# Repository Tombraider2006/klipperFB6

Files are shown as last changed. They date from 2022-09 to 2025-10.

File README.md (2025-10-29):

<h3 align="right"><a href="https://www.tinkoff.ru/rm/yakovleva.irina203/51ZSr71845" target="_blank">ваше "спасибо" автору</a></h3>

[**Мануал для тех кто только получил принтер**](/tune-up/newby.md)

[**Что Купить**](what_2_buy/readme.md) всё что надо для того, чтобы принтер  вас любил.

 [**Мануалы по настройке**](tune-up/readme.md) если возник вопрос "как  настроить"  вам сюда. *(фаза активного наполнения.)*

*<h2>**Модификации**</h2>*

   [**Nano4 v3.2 - GD32+CH340, "красная плата"**](GD32.md) - инструкции, марлин. правки под клиппер!

1. [**Marlin 2.1**](marlin/readme.md) модифицированные прошивки марлин, чтоб было на что откатиться, если не понравился klipper.

2.  [**drivers_uart**](https://github.com/Tombraider2006/klipperFB6/tree/main/drivers_uart)
    мануал по распайке драйверов по юарт для платы MKS Robin Nano v4 3.1. избавляемся от ора моторов на высоких скоростях  
3.  [**mcu_uart**](https://github.com/Tombraider2006/klipperFB6/tree/main/mcu_uart)   наглядно о подключении orange pi 3 lts к плате принтера по uart(чтоб провода наружу не торчали)
4.  [**Управление питанием системы, содержащей одноплатный компьютер Orange Pi3 LTS**](https://github.com/evgs/OrangePi3Lts/tree/main/power) 
 
5.  [**bme280**](https://github.com/Tombraider2006/klipperFB6/tree/main/bme280)
     Подключение датчика температуры BME280

6. [**подключение i2c датчиков к плате принтера**](i2c_mcu/readme.md) bme280, lm75a, ht21d и другие.
  
7.   [**clean_nozle**](https://github.com/Tombraider2006/klipperFB6/tree/main/clean_nozle)
     монтаж щетки очистки сопла, модель, макрос.
  
8. [**placement**](https://github.com/Tombraider2006/klipperFB6/tree/main/placement)
   Вариант размещения оборудования внутри принтера. там же необходимые модели для этого.
 
9. [**led_rgb**](https://github.com/Tombraider2006/klipperFB6/tree/main/led_rgb)   Подключение адресной светодиодной ленты к плате принтера

  1. [**Расширение памяти на Orange Pi 3 LTS (и не только)**](https://telegra.ph/Edit-01-28-2) 

   2.  [**Перенос файлов Gcode с внутреннего носителя OrangePi на внешнюю SD карту**](https://telegra.ph/Perenos-fajlov-Gcode-s-vnutrennego-nositelya-OrangePi-na-vneshnyuyu-SD-kartu-02-02)

 8.  [**распиновка платы**](https://github.com/makerbase-mks/MKS-Robin-Nano-V3.X/tree/main/hardware/MKS%20Robin%20Nano%20V3.1_001) - да она под сьемные драйвера в остальном сопадает с мишко6. использовать когда надо узнать какой пин в клиппере написать.
8.   [**Перевод стола на 220V**](/bed220.md)
быстро греем стол медвежонка

*<h3>**Модификации Экструдера**</h3>*

1.  [**biqu_h2**](karas/readme.md)
Модель каретки под экструдер biqu_h2 для FlyingBear Ghost 6.
 Уже 3 версии: под 4010 и 5015 кулеры и Deep версия. Добавлена версия под **V2VS**
1. [**Shark Extruder**](https://github.com/Chiffa-C3/Shark-Extruder) Экструдер разработанный для замены стандартного на принтере FBG6. Используется родной мотор и распространенные запчасти от BMG, встает на родную голову без ее переделок.
2. [**Замена каретки и установка Sailfin Экструдера**](https://youtu.be/aw4aZP5nTXc)
    Под видео есть ссылки на все необходимые файлы и запчасти.

3. [**Голова v2 от RuLED74 на FBG6.**](RuLED74_head_FBG6.rar) E3D V6 хотенд радиатор с гайкой, mrf экструдер(он же sailfin) под круглый мотор, предусмотрен монтаж 3d touch

4. [**Установка E3D V6 хотенда**](https://youtu.be/zrmbZkC-GsI) 
   Новая голова для 6ого призрака от летающих медведей для установки  радиатора e3d с креплением гайкой. Позволяет использовать в дальнейшем распространенные резьбовые термобарьеры. Так же немного переделаны сопла обдува модели, теперь они съемные и не будут мешать, при обслуживании хотенда.
5. [**Проект "Оливье"**](https://telegra.ph/Pechatayushchaya-golova-Olive-12-22) 

6. [**Проект "ZOHAN"**](https://www.thingiverse.com/thing:5883228)
   
   6.1 [**Фидер для ZOHAN**](https://www.thingiverse.com/thing:6153869)  фидер "жучок" из сток шестерёнок остатков набора бмг и двух вентиляторов 4010

7. [**bl-touch**](bltouch/readme.md) варианты крепления датчика на стоковую голову и на BIQU

8. [**FBG6-Condor**](https://github.com/Chiffa-C3/FBG6-Condor) Проект головы "Кондор" с поддержкой датчика Klicky-Probe

9. [**Заказать печатные детали из композита можно здесь**](https://vk.com/enot774rus)

  *<h4>**Про акселерометр**</h4>*

  1. [**Как перестать беспокоится и научится читать графики акселерометра**](accel_graph/readme.md)

 1.  [**adxl345_2_mcu**](https://github.com/Tombraider2006/klipperFB6/tree/main/adxl345_2_mcu) 
    способ подключения акселерометра к плате принтера.

1. [**ADXL 2 orange pi**](https://fdmprint.ru/2022/11/02/podkljuchenie-adxl345-akselerometr-i-orange-pi-3-lts/)
   Подключение акселерометра к OrangePi 3LTS [добавка если не получилось с alt2](adxl345_2_mcu/SPI-CS-FIX.md)

2. [**raspbery pi и ADXL345**](https://telegra.ph/Druzhim-raspbery-pi-s-ADXL345-04-25)Подключение акселерометра к Raspberry PI 

3. [**atmega168-klipper**](https://github.com/iliarub/atmega168-klipper)  ADXL через ардуино

4. **глюки spi** при подключении акселерометра можно устранить по [этому мануалу](https://github.com/orangepi-xunlong/wiringOP) (обычно глюк в 24 не работающем пине исправляется установкой этого git и командой  sudo gpio mode 15 ALT2 

5.[**Настройка Input Shaping в прошивке Marlin**](https://telegra.ph/Nastrojka-Input-Shaping-v-proshivke-Marlin-dlya-Flying-Bear-GHOST-6-02-15) 

*<h2>**Klipper**</h2>*

 1. [**Klipper на Orange Pi3 LTS - легко и быстро**](https://github.com/evgs/OrangePi3Lts/blob/main/sd_images.md) Здесь выложены предварительно настроенные образы Linux (Armbian и Debian) для Orange Pi3 LTS с уже установленным Klipper. Пользователю остаётся только настроить сеть и записать printer.cfg, соответствующий его 3д-принтеру.
 
 2.  [**Настройка Klipper для 3D-принтера FlyingBear Ghost 6 с подключением по USB**](klipper.md) 
 мануал  для совсем новичков, написан при моем содействии.(устарело)

 1. [**klipper_config**](https://github.com/Tombraider2006/klipperFB6/tree/main/klipper_config)
 
    в папке конфиг клиппера на flying bear ghost 6 
  подходит для стокового принтера без доработок, также есть закомментированные разделы небольших доработок. в комментариях файла config.cfg  есть какие то пояснения. читайте внимательно.
*не нужно бездумно копировать всю папку, вам нужен только [конфиг](klipper_config/printer.cfg) остальные файлы просто для сравнения со своими когда вам это будет нужно.*
 3. [**Удаленное управление Klipper**](https://telegra.ph/Udalennoe-upravlenie-Klipperom-cherez-privychnye-interfejsy-04-24)
 4. [**хорошее wiki по клипперу**](https://klipper.wiki/ru/home/initial/peripheral) 
     когда мне лень писать и я пишу что посмотрите сами, лезьте на этот ресурс вероятнее найдете подробную инструкцию

 5. [**wiki по телеграм боту**](https://github.com/nlef/moonraker-telegram-bot/wiki).

6. [**Установка  телеграмм бота на русском**](https://fdmprint.ru/2022/11/03/klipper-telegram-bot-easy/)
   
     конфиг файл бота для  мишки 6 можно скачать [тут](klipper_config/telegram.conf) кладем в папку конфигов не забываем вписать свои данные.

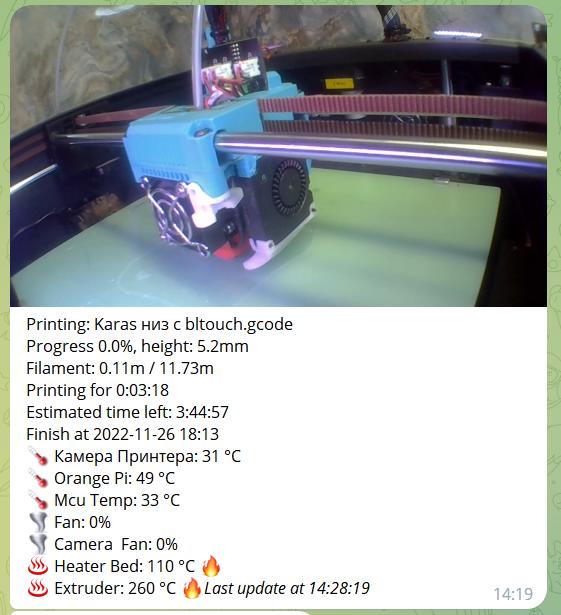
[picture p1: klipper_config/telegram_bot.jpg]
     
7. [**График шейперов сразу в телеграм бот**](/macros/telegram_adxl.md) читаем - делаем,наслаждаемся.

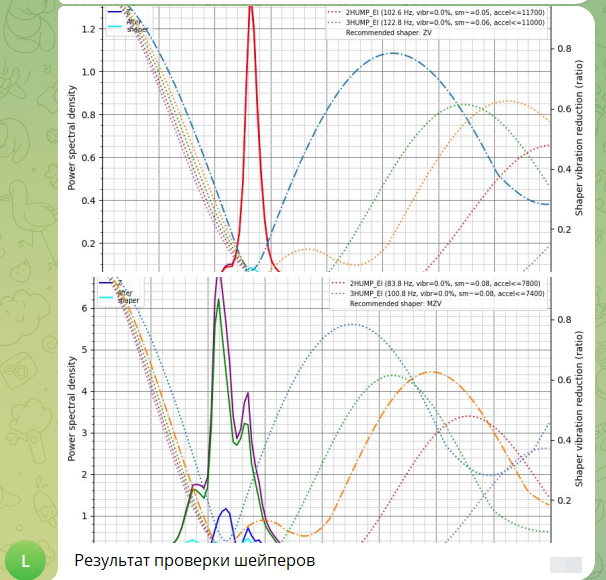
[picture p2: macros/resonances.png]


2. [**Плагин для слайсера CURA с настройками klipper**](https://github.com/jjgraphix/KlipperSettingsPlugin)

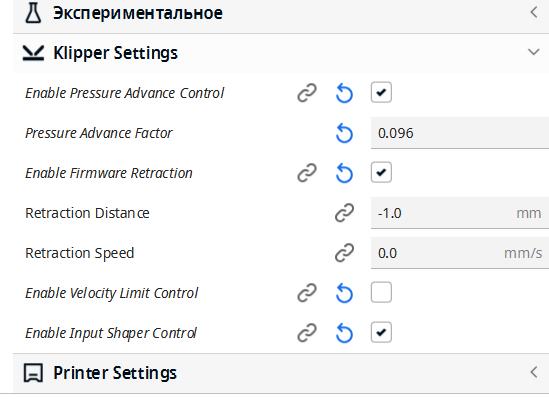
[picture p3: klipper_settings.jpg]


1. Чтобы не бегать с флешкой в Cura есть плагин **Moonraker** ищется через магазин. в нем пишем адрес принтера добавив к нему порт 7125 получится как то так http://ip_printer:7125/  в строке нижней пишем 15 секунд на ожидание ответа от сервера. картинки подключения посмотреть [тут](moonraker.jpg) и [тут](moonaker1.jpg)

 [**Макросы**](macros/readme.md) нужные и не очень

*<h3>**Про экран, стоковый и не только**</h3>*

  Моя рекомендация поставить [7 дюймовый экран](https://www.thingiverse.com/thing:5629418) убрав стоковый

   1. [**Klippersreen**](klippersreen/readme.md) 
Если не запустился сразу *покупной* экран 5 или 7 дюймов.

      2. **Клипперскрин** подключение штатного экрана по [этому мануалу](https://sergey1560.github.io/fb4s_howto/mks_ts35/) в родном мануале совсем невнятная схема подключения [тут](TS35%20Klipper.pdf) тоже самое но чуть понятнее. [**Плата для подключения штатными проводами экрана к вашей PI**](https://github.com/evgs/kross-pi-hat)
      
      3. [**Повышение скорости работы MKS TS35-R**](https://github.com/evgs/OrangePi3Lts/tree/main/fb-st7796-fast)  Актуально для OrangePi3 LTS. На Raspberry PI экран и так работает на высокой частоте SPI

      3. [**Klipper: Debian + KlipperScreen + Экран СТОК FB Ghost6 + MKS TS35-R V2.0**](https://fdmprint.ru/2022/11/19/klipper-debian-klipperscreen-ehkran-stok-fb-ghost6-mks-ts35-r-v2-0/)

      4. **Клипперскрин** если у вас raspberry [тут](https://github.com/willngton/3DPrinterConfig/blob/main/mks_ts35/mks_ts35_guide_archived.md) или [тут](https://github.com/evgs/FBG6-Klipper/blob/main/Klipperscreen-RPI.md)
      5. [**Клипперскрин** на телефоне](https://telegra.ph/KlipperScreen-na-starom-android-telefone-12-16)
   
      6. [**Еще одно руководство по установке клипперскрин на телефон**](https://telegra.ph/KLIPER-NA-ANDROID-TELEFON-03-01)
   
      7. [**Проект "Чувырла"**](chuvir_screen/readme.md) крепление экрана и видеокамеры на место штатного экрана.
     
      8. [**4.3" экран с креплением камеры**](https://www.thingiverse.com/thing:5762517) от наших итальянских пользователей.

*<h2>**остальное**</h2>*

1. [**Охлаждение стола для FBG6**](https://3dtoday.ru/blogs/viknikvvk/oxlazdun-dlya-letayushhego-miski)

2. [**Усиление крепления стола спереди дополнительными валами**](https://www.thingiverse.com/thing:5994260)

3. [**Вариант усиления консольного стола FlyingBear Ghost6 дополнительными валами и двигателем оси Z**](https://www.printables.com/model/1063427-flyingbear-ghost6-auxiliary-z-axis-upgrade) 

4. [**крепление для пишки на магнитах**](https://www.thingiverse.com/thing:5686745) 

5.  [**Автоперезапуск сервиса klipper после включения принтера**](https://mirv.top/2021/10/08/avtoperezapusk-servisa-klipper-posle-vklyucheniya-printera/)

 *<h3>**про камеру**</h3>*
 1. [**ustreamer**](https://fb-waiters.bibirevo.net/klipper/ustreamer#zachem_i_pochemu) 
 Замена\Установка стримингового модуля. Так как mjpg-streamer умер на данный момент, а камеру хочется, читаем, ставим. если что то непонятно есть альтернативный источник [тут](https://fdmprint.ru/2022/11/10/klipper_ustreamer/)

 2.[**Logitech C270 с М12 широкоугольным объективом**](https://telegra.ph/Logitech-C270-s-M12-shirokougolnym-obektivom-03-19) инструкция валидна , [**более правильная модель корпуса**](https://www.thingiverse.com/thing:6440452)

 3. [**RTSP IP камера и Klipper**](https://flyingbear.info/firmware/klipper/IPcam_to_Klipper)

1. **timelapse здорового человека** 

   Многие пользуются функцией таймлапсов которые предоставляет телеграм бот но он ограничен в функионале и не позволяет делать красиво.
если хотите получить действительно хорошие видео рекомендую [вот этот плагин](https://github.com/mainsail-crew/moonraker-timelapse) есть отвод головы на время сьемки кадра, переменный целевой fps и многое другое. посмотрите страничку авторов на гитхабе - не пожалеете. Или читайте инструкцию по установке [тут](https://fdmprint.ru/2022/11/24/klipper-timelapse-intervalnaja-semka-ustanovka-nastrojjka-moonraker-timelapse/)

[**Flyingbear.info**](https://flyingbear.info/firmware/klipper/klipper_more)- полезный ресурс от 5 мишки, там про то как настроить например вебкамеру и не только. многое подойдет на 6 мишку если не забывать что у нас разные платы)

 [**телеграм чат FB6 владельцев и Reborn2**](https://t.me/fbg6_s) где есть многое, если не всё для владельца flying bear ghost 6  он же просто мишка 6. 

`Ставьте звездочку проекту, так будет проще находить владельцам принтера нужную информацию`

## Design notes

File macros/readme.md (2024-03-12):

# Макросы в одном месте

Конечно можно пихать все макросы в основной файл `printer.cfg` но через какое то время вы там совсем потеряетесь. Поэтому лучше добавить строчку `[include имя_файла.cfg]` в любом месте вашего `printer.cfg` где всегда можно отключить или включить его. можно создать папку с макросами и сделать изящнее `[include macros/*.cfg]` и все файлы оттуда будут добавляться в вашу конфигурацию как бы вы их не назвали.

## График шейперов сразу в телеграм бот 

[telegram_adxl.md](telegram_adxl.md) читаем - делаем,наслаждаемся.



> **Ahtung! Attention! Внимание!**
> если есть имена например подсветки в макросе, то они должны совпадать с вашими именами в конфигурационном файле. Читайте документацию!

## Смена Филамента

Чтобы делать полосатенькие модели например так:

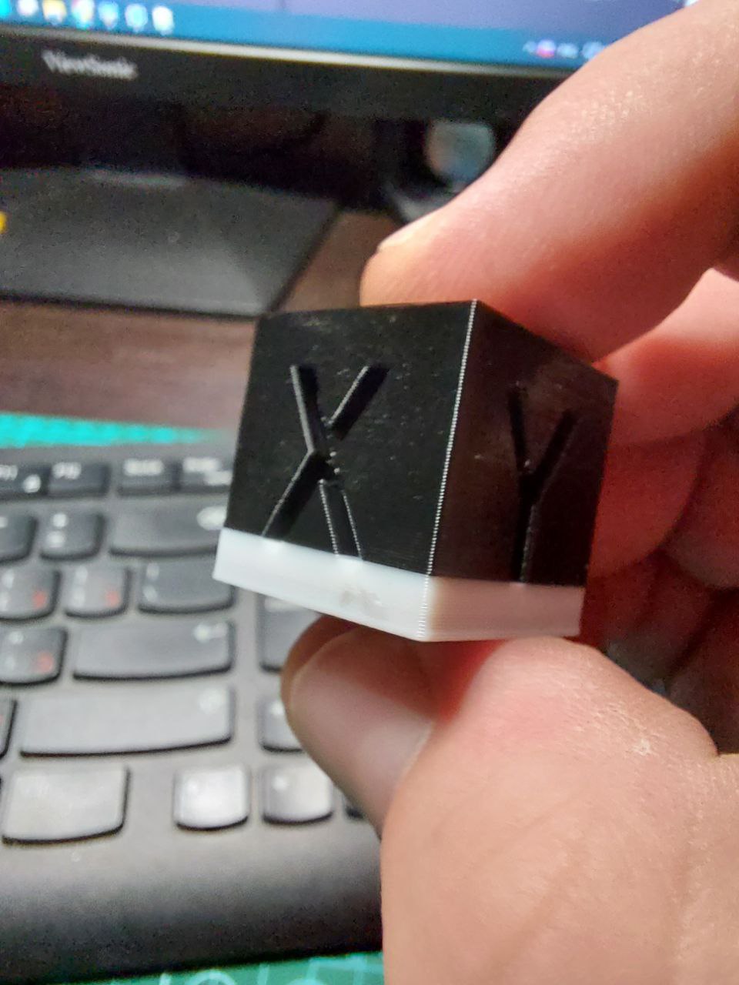
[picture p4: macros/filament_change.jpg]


Варианты:
- [Для стоковой головы FB6](filament.cfg)
- [Для biuu_h2](filament_biqu.cfg)

Составной макрос смены филамента. Ставит на паузу PAUSE, вызывает макрос FILAMENT_UNLOAD для выгрузки филамента, подаёт звуковой сигнал BEEP, COUNTDOWN ждёт 5 минут, пока вы заправите новый филамент в фидер, снова подаёт звуковой сигнал и FILAMENT_LOAD загружает филамент, RESUME запустит печать дальше, если макрос был вызван в процессе печати, например из G-code.

у мишки6 для   [BEEP макроса (скачиваем)](beep.cfg) используется та самая красная лампочка "ханасвист". чтобы ее активировать у вас должен быть раздел в `printer.cfg` если его нет добавляем:
```gcode
[output_pin _Zummer] 
pin: PA2 
```

## Чистка сопла

Этот макрос подьезжает к определенному месту и водит туда сюда по латунной щетке, [подробнее тут](../clean_nozle/readme.md) Быстро скачать [тут](clean.cfg)

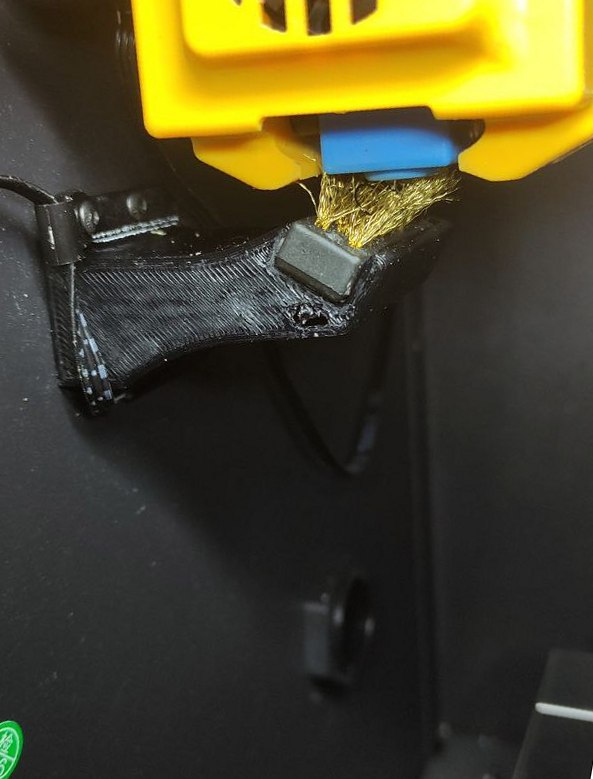
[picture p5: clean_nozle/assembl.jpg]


## Макросы для RGB подсветки

подробнее [тут](../led_rgb/readme.md)

Скачать одним файлом можно [тут](led.cfg)

 

## Адаптивная сетка для стола

 Это почти как обычная сетка для стола, но только "где" и "когда" это необходимо. Иногда я печатаю мелкие детали, иногда печатаю целые пластины, и мне нравится получать точную кровать_сетку (например, 9x9 или больше). Однако это занимает много времени и бесполезно прощупывать всю пластину только на небольшой части посередине. Здесь помогает адаптивная сетка кровати. подробнее [тут](https://github.com/Frix-x/klippain/blob/main/docs/features/adaptive_bed_mesh.md)

## Измерение вибрации

Описание(перевод с гита)

У меня были сильные вибрации на очень специфических скоростях на моей машине (например, 52 мм / с), и я хотел найти все эти проблемные скорости, чтобы избежать их в моем профиле слайсера и, наконец, получить бесшумную машину, о которой я мечтал!

Это полностью автоматизированный рабочий процесс, который работает путем перемещения головки инструмента при использовании акселерометра:

1. Он выполняет последовательность движений по оси, которую вы хотите измерить, с различными настройками скорости, при этом регистрируя глобальные вибрации машины с помощью акселерометра.
Затем он вызывает автоматический скрипт bash, который автоматизирует несколько вещей:
1. он генерирует график вибраций для указанной оси с помощью пользовательского скрипта Python.
Затем он переместит график и связанный с ним архив CSV в папку результатов ADXL .
1. он управляет папкой, чтобы удалить старые файлы и сохранить только набор (по умолчанию три) самых последних результатов.
2. Результаты можно найти в папке результатов ADXL , которая находится непосредственно в корне папки конфигурации, чтобы **обеспечить доступ непосредственно из вашего браузера с помощью файлового менеджера FLuidd/Maisail. SSH не нужен!**
подробнее [тут](https://github.com/Frix-x/klippain/blob/main/docs/features/vibr_measurements.md)

~~в апельсинке есть баг обработки скрипта. добавили паузу при обработке, скачать модифицированный [plot_graphs.sh](../klipper_config_my/scripts/plot_graphs.sh)~~

прочитать про все функции скрипта [тут](https://github.com/Frix-x/klippain/blob/main/docs/features.md)

## Восстановление печати после сбоя питания 

[power_loss.cfg](power_loss.cfg) на данный момент не проверен, стырен [тут](https://github.com/CODeRUS/klipper_config/blob/rumba32/power_loss_simple.cfg)

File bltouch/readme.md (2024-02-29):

[**Вариант монтажа на стоковую голову**](https://www.thingiverse.com/thing:5660302)

[**модель крышки на стоковую голову с креплением под BIQU MicroProbe и с зауженными каналами обдува.**](https://www.printables.com/model/750766-fbg6-biqu-microprobe-mount)

[**Вариант монтажа на стоковую голову продвинутый**](https://www.thingiverse.com/thing:5744744)

Конфиг необходимо править с учетом отступов от сопла до точки замера блтач.!

**Данный конфиг верен для версии головы KARAS_4010 c экструдером BIQU H2 V2**

**Монтаж:**
Подключается в самый нижний левый на плате на нем написано bl-touch, (верхний-сигнал, средний-"+", нижний-земля) который не видно и в концевик "H"(это датчик огня не нужный). контакты концевика (средний-земля, верхний-сигнал).  

**Настройка:**
в секцию `[stepper_z]` необходимо найти исправить!(например видим `endstop_pin: !PC8` исправляем на `#endstop_pin: !PC8`) следующие строки чтобы они выглядели так:

```
#endstop_pin: !PC8 
endstop_pin: probe:z_virtual_endstop
#position_endstop: 0.5
```
(*Внимание! у вас в конфиге уже может быть раздел bed_mesh - его ищем\удаляем и потом вписываем этот*  так же возможно в разделе автоматической настройки  там где "#*#" ищем safe_z_home тоже удаляем )

Создаем новый раздел и вписываем это:

```
[bltouch]

sensor_pin: ^PC4
control_pin: PA8
y_offset: -17.85
z_offset: 2.0
x_offset: 22.65
speed: 10.0
samples: 2
samples_result: median
sample_retract_dist: 3.0
samples_tolerance: 0.1
samples_tolerance_retries: 1

[safe_z_home]
home_xy_position: 105,121                                                       # CAUTION! Depends on probe X/Y offset
z_hop: 10
move_to_previous: True                                                       # Return back ~X0/Y0 after Z0 at center
z_hop_speed: 10
speed: 50
[gcode_macro G29]
gcode:
    BED_MESH_CLEAR
    G28
    BED_MESH_CALIBRATE
    BED_MESH_PROFILE SAVE=name
    SAVE_CONFIG
    BED_MESH_PROFILE LOAD=name

[bed_mesh]
speed: 40
horizontal_move_z: 5 # отступ во время проб по оси Z
mesh_min: 30,10 # CAUTION! = probe_xy = nozzle_xy + offset_xy
mesh_max: 245,185 # стол с учетом сдвига на bltouch
probe_count: 6,4 # здесь мы ставим количество точек проб по икс и по игрек
algorithm: bicubic
fade_start: 1 #на какой высоте начнем выравнивать модель
fade_end: 10 #на этой высоте в мм закончим выравнивать.

[screws_tilt_adjust] # = nozzle_xy = probe_xy - offset_xy
screw4: 5,30 
screw4_name: front left screw
screw1: 210,25
screw1_name: front right screw
screw2: 210,202 
screw2_name: back right screw
screw3: 5,202
screw3_name: back left screw
speed: 100
screw_thread: CW-M4
```
**Как настроить:**

Хоуминг в центре стола, потом двигаете туда сопло, в центр и добиваетесь зазора с которым обычно печатаете. Полученную разницу с нулём по Z вычитаете из того Z-офсет который стоял) по умолчанию ставил 2мм - норм.  И точная калибровка зазора делается при печати, просто ручками подбираее Z-офсет в клиппере и потом опять таки вычитаете из Z-офсета конфига.

**Как проверить отступ датчика от сопла:**(НЕОБЯЗАТЕЛЬНЫЙ ПУНКТ)
положите лист бумаги на стол, прижать прищепками, выровняв по краю. переместить голову над листом и карандашиком отметить где сопло, где кончик датчика. Потом снять лист, померять отступы от сопла.

Юстировка через klippersreen:

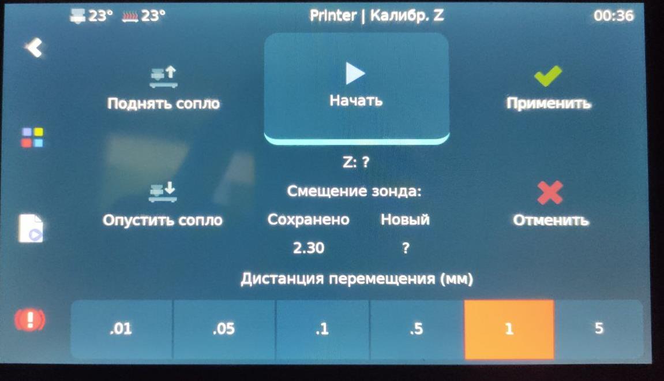
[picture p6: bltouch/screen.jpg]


калибровка стола:

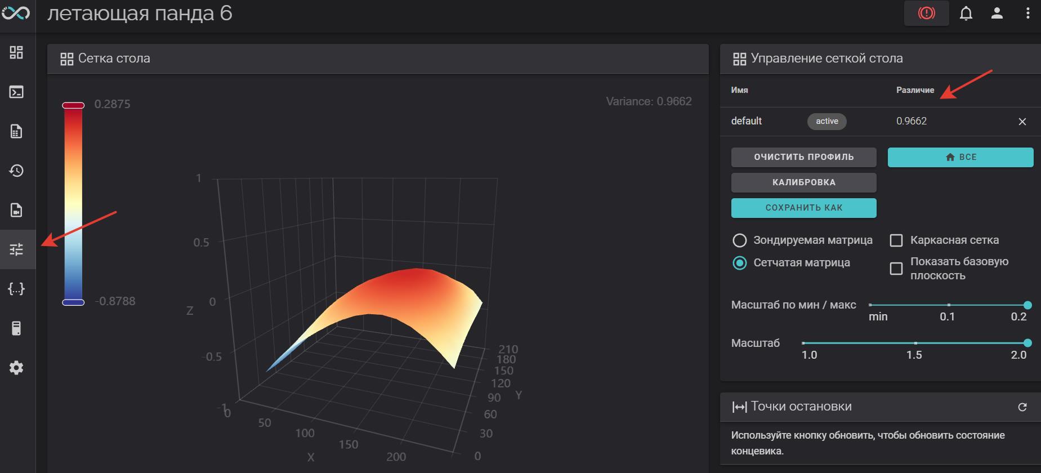
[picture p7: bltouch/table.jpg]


**Настройка винтов по датчику:**
01:20 означает 1 полный оборот и 20 минут по часовой стрелке СW= по часовой стрелке. CCW = против часовой стрелки. 

Очень удобная штука, винты настроить стало гораздо проще.
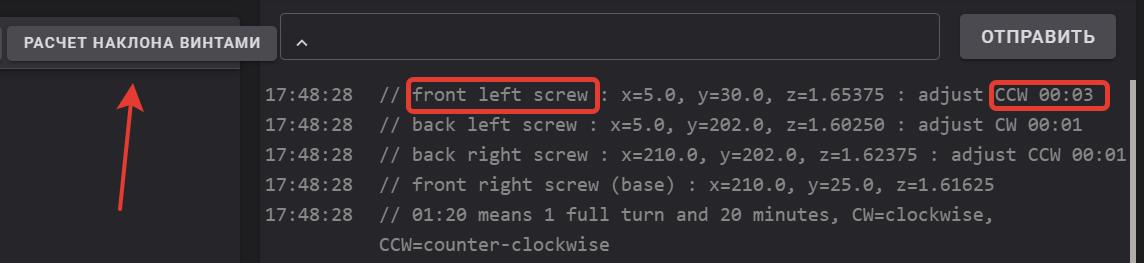
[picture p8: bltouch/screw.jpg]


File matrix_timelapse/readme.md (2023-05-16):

**Таймлапс в стиле фильма матрица** *в разработке*



Если вы уже прошерстили мой Гит вы наверняка уже обзавелись модулем таймлапса но есть у него один недостаток, снимает он с одного ракурса и вот данный раздел призван этот недостаток устранить. 

На данный момент  проект признан жизнеспособным, осталось только твердотельное моделирование и обкатка.

Для реализации нам понадобиться серво самая простая. sg90 подойдет.  в дальнейшем планирую использовать на 270 грудусов, сейчас пока на время разработки используется 180 градусов, подключить ее достаточно просто, у нее три вывода G - земля, VC  5 вольт, и сигнал. ничего не напоминает? да, это практически любой разъём в нашей плате) я использовал `PA8` 3d touch. 

желтый провод сигнал красный 5 вольт и черный или коричневый земля.  цепляем к принтеру. 
в printer.cfg добавляем раздел:

```
[servo matrix]
pin: PA8 #  пин на плате
maximum_servo_angle: 180 # градус сервы
minimum_pulse_width: 0.0008 # по умолчанию 0.001 тут можно поиграться когда серва не поворачивается на полную
maximum_pulse_width: 0.0025 # по умолчанию 0.002 важно не только уменьшать но и увеличивать. тоесть играем парой значений одновременно
initial_angle: 0 # не меняем. это стартовый угол при загрузке принтера
```
После того как подсоеденили и прописали можем проверить. В консоли принтера пишем: `SET_SERVO SERVO=matrix ANGLE=90` дальше пробуем максимальные углы, меняем размер импульсов. для этого можно использовать команду  `SET_SERVO SERVO=matrix WIDTH=0.001`  значения выбирайте сами,  0 выключит серву и можно подвигать руками...

Как наиграетесь можно написать макрос. у меня в `printer.cfg` есть строчка `[include macro.cfg]` и рядышком файл рядышком с таким же именем macro.cfg куда я записываю макросы чтоб они мне не мешали читать конфиг в минуты раздумий)

Итак макрос нам нужен для того чтобы посчитать общее количество слоев и номер текущего слоя  и вычислить градус на какой повернуть серву чтобы вначале был 0, а в конце 180\270 градусов соответсвенно.  спасибо неравнодушным людям которые за несколько потных дней сваяли нам вот такой макрос:

```gcode
[gcode_macro BEGIN_LAYER]
description: Start a new layer and notify system
gcode:

  {% set CUR  = params.NUM|default(0)|float + 1 %}
  {% if params.COUNT and params.COUNT != 0 %}
        {% set TOTAL = params.COUNT|default(0)|float %}
  {% elif printer["gcode_macro middle"].total_layer and printer["gcode_macro middle"].total_layer!= 0 %}
        {% set TOTAL = printer["gcode_macro middle"].total_layer %}
  {% else %}
         { action_respond_info("COUNT of Total layers is required!") }
  {% endif %}

  SET_GCODE_VARIABLE MACRO=middle VARIABLE=cur_layer VALUE={CUR}
  SET_GCODE_VARIABLE MACRO=middle VARIABLE=total_layer VALUE={TOTAL}
  {action_respond_info("BEGIN CUR: %s TOTAL: %s" % (CUR, TOTAL))}

[gcode_macro middle]
description: Variable_storage
variable_cur_layer: 0
variable_total_layer: 0
gcode:
#    {action_respond_info("MIDDLE TOTAL: %s TOTAL: %s" % (CURRENT_LAYER, TOTAL_LAYER))}

[gcode_macro MATRIX]
gcode:
    {% set CURRENT_LAYER = printer["gcode_macro middle"].cur_layer %}
    {% set TOTAL_LAYER = printer["gcode_macro middle"].total_layer %}

    {% set angle_move = 180 / TOTAL_LAYER * CURRENT_LAYER %} #задаем переменную сдвига на слой. вот здесь и задаем свою серву 180 или 270 градусов.
 #   { action_respond_info("MATIRIX TOTAL: %s CUR: %s" % (TOTAL_LAYER, CURRENT_LAYER)) } #вывод в консоль текущего слоя и всего слоев
 #   { action_respond_info("angle %s" % angle_move) } # вывод в консоль текущего угла
    SET_SERVO SERVO=matrix ANGLE={angle_move} #4 макрос сдвига
```
Для того чтобы он заработал нам необходимо сделать так чтобы слайсер нам посылал номера слоеев и их общее количество. (*найдутся умники которые мне скажут что клиппер и так знает количество слоев но это не так, достаточно часто цифры там могут быть сильно далеки от реальных.*) 

В Cura нам надо найти раздел Расширения > Пост-обработка Изменить G-код.

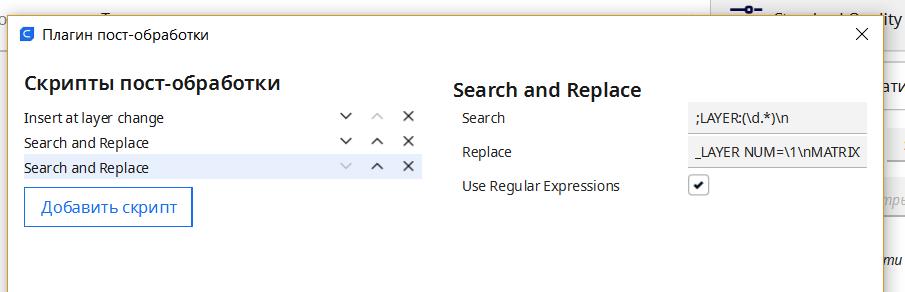
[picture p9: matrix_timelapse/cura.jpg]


Найти раздел `search and replace` и вписать в первую строчку:
`;LAYER_COUNT:(\d.*)\n` 

а во вторую: `;LAYER_COUNT:\1\nBEGIN_LAYER COUNT=\1\n`

Не забываем ставь галочку как на картинке "использовать регулярные выражения"

теперь открываем еще раз `search and replace` 

и теперь в первую строку копируем это: `;LAYER:(\d.*);\n`

во вторую это: `;LAYER:\1;\nBEGIN_LAYER NUM=\1\nMATRIX\n`

Если у вас Prusa Slicer:

в раздел **before layer change G-code** вписать:
``` 
BEGIN_LAYER NUM={layer_num} COUNT={total_layer_count};
matrix;
```
Нарезаем модель, радуемся. 
Для того чтобы всё это заработало нам нужна модель. 
А вот её как раз нет) ждемс или моделируем сами)

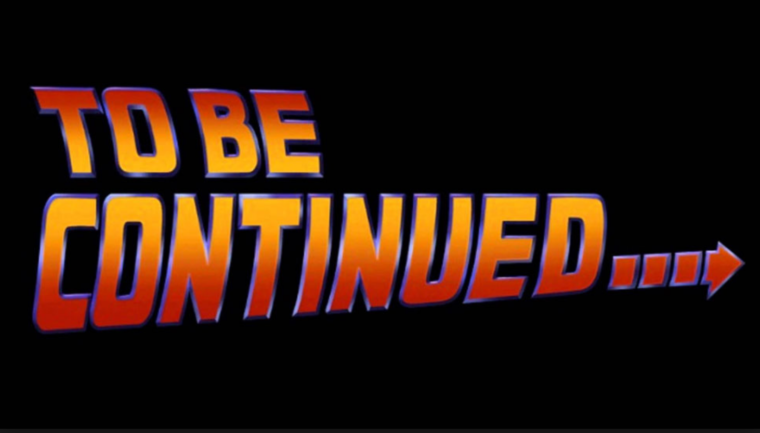
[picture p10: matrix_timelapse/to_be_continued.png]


TEST!!! NOT USE!!!!!

тест, не трогать не использовать. деальнейший код просто обсуждение разработки!!!!

```extratmc
[manual_stepper matrix]
step_pin: PD15
dir_pin: PA1
enable_pin: !PA3
microsteps: 16
rotation_distance: 5.625
full_steps_per_rotation: 200
velocity: 15
accel: 1000
#endstop_pin: !PC8 # раскоментировать при наличии концевика
position_max: 455 # надо померять расстояние и поставить чуть меньше

[gcode_macro BEGIN_LAYER]
description: Start a new layer and notify system
gcode:

  {% set CUR  = params.NUM|default(0)|float + 1 %}
  {% if params.COUNT and params.COUNT != 0 %}
        {% set TOTAL = params.COUNT|default(0)|float %}
  {% elif printer["gcode_macro middle"].total_layer and printer["gcode_macro middle"].total_layer!= 0 %}
        {% set TOTAL = printer["gcode_macro middle"].total_layer %}
  {% else %}
         { action_respond_info("COUNT of Total layers is required!") }
  {% endif %}

  SET_GCODE_VARIABLE MACRO=middle VARIABLE=cur_layer VALUE={CUR}
  SET_GCODE_VARIABLE MACRO=middle VARIABLE=total_layer VALUE={TOTAL}
  {action_respond_info("BEGIN CUR: %s TOTAL: %s" % (CUR, TOTAL))}

[gcode_macro middle]
description: Variable_storage
variable_cur_layer: 0
variable_total_layer: 0
gcode:
#    {action_respond_info("MIDDLE TOTAL: %s TOTAL: %s" % (CURRENT_LAYER, TOTAL_LAYER))}

[gcode_macro MATRIX]
gcode:
    {% set CURRENT_LAYER = printer["gcode_macro middle"].cur_layer %}
    {% set TOTAL_LAYER = printer["gcode_macro middle"].total_layer %}

    {% set angle_move = 450 / TOTAL_LAYER * CURRENT_LAYER %} #задаем переменную сдвига на слой.  первая цифра максимальное расстояние по балке
 #   { action_respond_info("MATIRIX TOTAL: %s CUR: %s" % (TOTAL_LAYER, CURRENT_LAYER)) } #вывод в консоль текущего слоя и всего слоев
 #   { action_respond_info("angle %s" % angle_move) } # вывод в консоль текущего угла
    MANUAL_STEPPER STEPPER=matrix MOVE={angle_move} SPEED=5 #4 макрос сдвига

```

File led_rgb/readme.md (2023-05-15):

**Установка адресной светодиодной ленты.** 

Недостатки штатной ленты принтера ясны каждому владельцу, черный цвет стенок, 
темная поверхность ультрабазы, эффективно поглощают свет и рассмотреть что-то, даже в свете ленты, которая светит абы как, достаточно проблематично.
К сожалению компактность корпуса и необходимость снимать боковую крышку сдвигом вниз, в случае нужды доступа к плате принтера, не позволяют закрепить ленты.
Поэтому решение комплексное и довольно накладное. первая часть описана в разделе  [placement](https://github.com/Tombraider2006/klipperFB6/tree/main/placement)  которая позволяет установить дополнительный блок питания и хост внутри корпуса.
 Вторая часть это подключение адресной ленты. для этого есть штатный разьем неопиксель *PE6* на плате. в который воткнута штатная подсветка, его и используем. 
 у меня было несколько этапов и я сделал два канала подключения. я задействовал штатный разьем для подключения подсветки в голову экструдера,
 а основной свет запитал из разьема 3d-touch *PA8* который все равно некуда сунуть с нашей компоновкой. Я опишу штатный случай и все дальнейшие инструкции для штатного разъема.
 
 **update** (*относится к платам от MKS*) по неопикселю есть лайфхак в виде подтягивающего резистора 4.7К, который ставится на ленту (или в разъём) между сигнальным проводом и +5В. (помечен звездочкой)
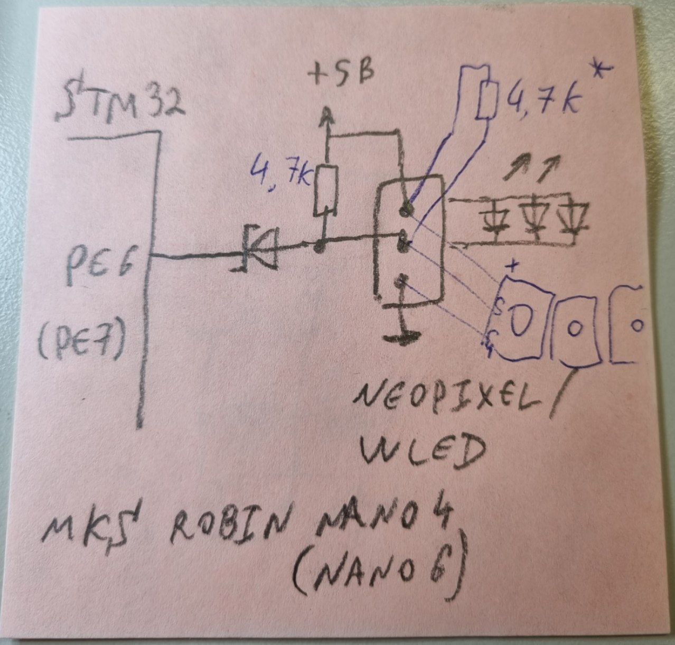
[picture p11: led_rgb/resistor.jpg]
 

 значок подтягивающего резистора в клиппере его не заменит, так как Во-первых, внутренняя подтяжка слишком слабая (~50К), во-вторых, не с той стороны относительно диода (на схеме). Без него напряжение нарастает недостаточно быстро и стабильность работы будет определяться только производителем неопикселей. После распайки резистора получится итоговое сопротивление меньше, ток больше, скорость нарастания напряжения увеличивается.

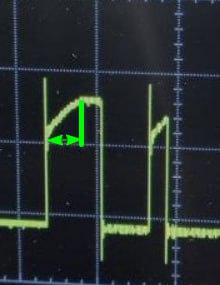
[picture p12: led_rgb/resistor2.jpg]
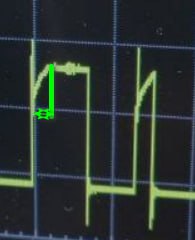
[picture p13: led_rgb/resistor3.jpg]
 

  **немного теории**
 
  Команды в ленте передаются от диода к диоду, паровозиком.
  У ленты есть начало и конец, направление движение команд на некоторых моделях указано стрелочками.
  Для примера рассмотрим ws2812b, у нее три контакта. Два на питание, а вот третий в начале ленты называется DI (digital input), а в конце – DO (digital output).
  Лента принимает команды в контакт DI! Контакт DO нужен для подключения дополнительных кусков ленты или соединения матриц.
  
  Если в схеме возможна ситуация, при которой на ленту не будет подаваться питание 5V,
  но будет отправляться сигнал с микроконтроллера – лента начнёт питаться от дата-пина.
  В этом случае может сгореть как первый светодиод в ленте, так и пин контроллера.
  Не испытывайте удачу, поставьте резистор с сопротивлением 200-500 Ом.
  Точность резистора? Любая. Мощность резистора? Любая. Да, даже 1/4.
  
   Самый важный пункт, который почему то все игнорируют: цифровой сигнал ходит по двум проводам, 
   поэтому для его передачи одного провода от ардуины мало. Какой второй? Земля GND.
  
  *Питание.* Один цвет одного светодиода при максимальной яркости кушает 12 миллиампер. 
  В одном светодиоде три цвета, итого ~36 мА на диод. 
  Пусть у вас есть метр ленты с плотностью 60 диод/метр,
  тогда 60на36 = 2.1 Ампера при максимальной яркости белого цвета, соответственно нужно брать БП, 
  который с этим справится. Также нужно подумать, в каком режиме будет работать лента. 
 
 Продолжая тему питания, хочу отметить важность качества пайки силовых точек (подключение провода к ленте, подключение этого же провода к БП), а также толщину проводов. Как показывает опыт, брать нужно провод сечением минимум 1.5 квадрата, если нужна полная яркость. Пример: на проводе 0.75 кв.мм. на длине 1.5 метра при токе 2 Ампера падает 0.8 вольта, что критично для 5 вольт питания. Первый признак просадки напряжения: заданный программно белый цвет светит не белым, а отдаёт в жёлтый/красный. Чем краснее, тем сильнее просело напряжение!
 
 *маленький лайфхак - если вы хотите просто попробовать и подключить только кусок ленты вместо штатного, то можно просто задействовать три провода от штатного места и избежать всех плясок с бубном с понижайкой и блоком питания. расчет простой если брать по моей ссылке это 0.2 ватта на диод. ватты это произведение тока на вольтаж. тоесть суммируем количество диодов получаем ватты делим на напряжение, если результат больше чем 0.5 Ампера идём за понижайкой или БП. В нашем случае не больше 12 светодиодов. Но это баловство, а не улучшение принтера* 

 **материалы и инструменты**
 
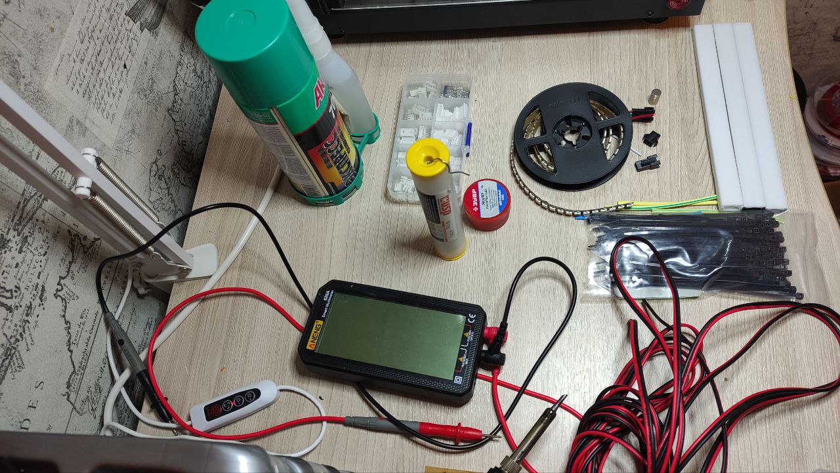
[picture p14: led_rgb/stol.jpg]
stol
 
 
 Нам понадобится:
 
 Распечатанные модели держателей ленты  [тыц](2_long_190mm.stl) и [тыц](1_long_190mm.stl)  млм  [альтернативный](Led_holder.stl)
 
 лента RGB 5v [например тут](http://alii.pub/6hwuel) 144 диода на метр  
 
 магниты неодимовые небольшие [например такие](http://alii.pub/6hwuj9)
 
 провода минимум сечения 0.5
 
 паяльник, припой, стяжки, кусачки, мультиметр, клей (суперклей или похожий)
 
 **Монтаж**

необходимо продумать как и где у вас будут стоять ленты чтобы паравозик сигнального провода не болтался в воздухе и по максимуму был коротким. 

У меня порядок такой: от платы к верхнему штатному месту, от него вниз к боковой стенке, от первой планке ко второй. был еще конец который уходил в правый угол но мне не понравилось как он светит и я его убрал. возможно верну позже.

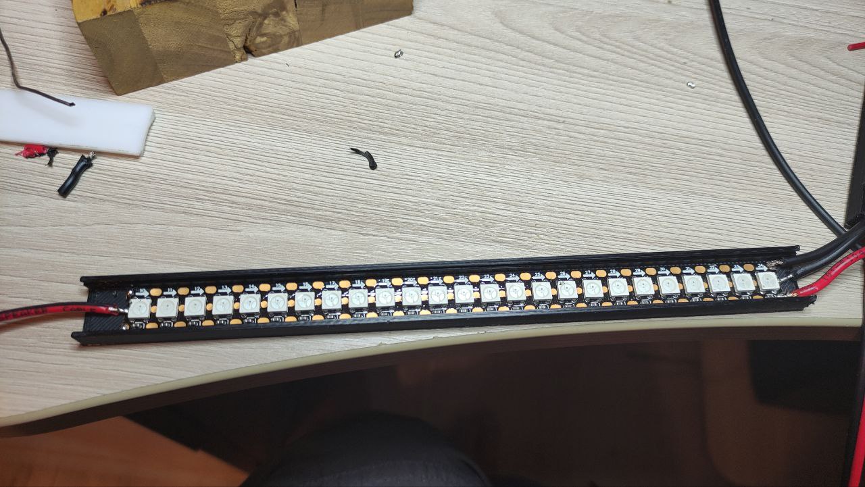
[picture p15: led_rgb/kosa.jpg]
фото косы

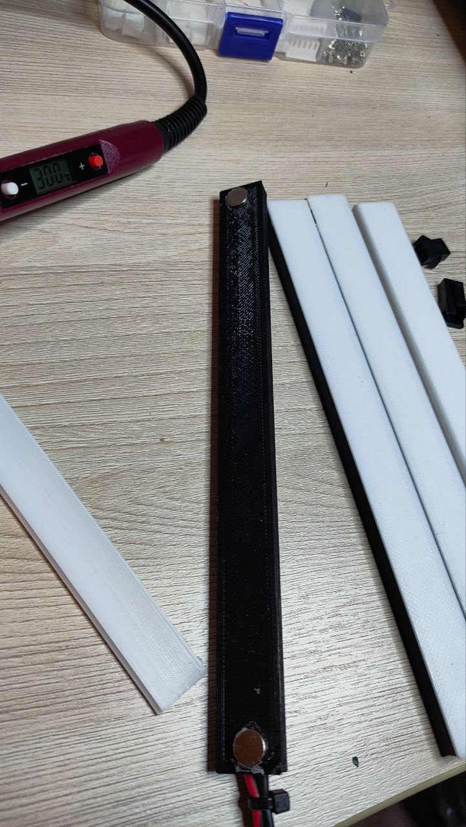
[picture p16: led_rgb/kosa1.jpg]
фото косы2


 Питание к ленте может подходить с любой стороны, хоть посреди ленты, а вот сигнальный провод строго паравозиком по стрелкам, у меня получилось запихать в один корпус 25 светодиодов и 27 на место штатной ленты. Площадку при пайке можно легко оторвать и поэтому на одной из лент у меня 24 светодиода)
 На штатное место подсветки модель площадки которую я дал **не подходит!** ее задевает голова, поэтому я ее просто приклеил на суперклей.
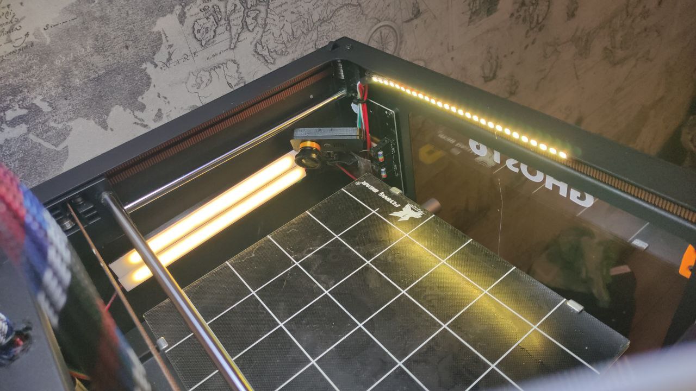
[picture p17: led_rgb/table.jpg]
итог
 

на плате не все так очевидно, посмотрите контакты остальных разьемов и контакты неопикселя..  итак нам нужны GND и PE6 

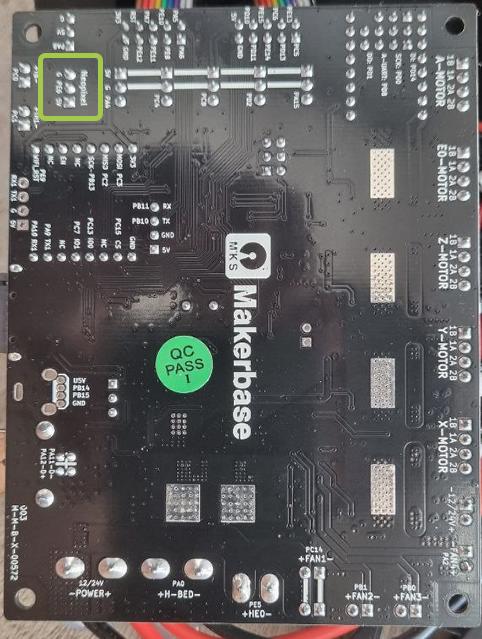
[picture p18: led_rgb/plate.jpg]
плата
 

подключаем их первой ленте и там же подключаем питание от блока питания.  дальше тянуть землю от платы не надо.  если вы соеденили GND платы и GND блока питания ранее то достаточно PE6

Дальше работа паяльником, клеем и укладка проводов, уверен, у вас получится красивиее чем у меня)

**Конфигурирование**

В ```printer.cfg``` необходимо найти и раскомментировать или вписать заново следующие строки. не забудьте закоментировать старые про стоковую ленту

```g-code
[neopixel my_neopixel] # вместо my_neopixel можете написать свое имя только вместо пробела, если он у вас будет в имени, используйте подчеркивание и не забудьте поменять имя в макросах.
pin: PE6 # наш пин 
chain_count: 75 #количество светодиодов всего во всей ленте
color_order: GRB

initial_RED: 0.5 # начальные значения при включения, у меня желтый цвет на половинной яркости 
initial_GREEN: 0.5
initial_BLUE: 0.0
initial_WHITE: 0.5
```

Теперь можно похулиганить. 

Добавим пару макросов
первый добавит макрос  PartyTime с ним ваши светодиоды будут красиво моргать разными цветами, расписано на 27 светодиодов. Можете заняться и расширить дальше методом индусского кода или написать свой) 

*важное замечание* добавьте этот макрос в часть неисполняемых при печати или просто не нажимайте его во время печати, это вызовет паузу печати на время выполнения макроса. *вот три раза написал "печати" и все равно найдется умник который нажмет...*

```g-code
[gcode_macro PartyTime]
gcode:
    {% for flashes in range(params.COUNT|default(10)|int) %}
        SET_LED LED=my_neopixel RED=0.0 GREEN=0.0 BLUE=0.5 INDEX=1 TRANSMIT=0
        SET_LED LED=my_neopixel RED=0.0 GREEN=0.0 BLUE=0.5 INDEX=2 TRANSMIT=0
        SET_LED LED=my_neopixel RED=0.0 GREEN=0.0 BLUE=0.5 INDEX=3 TRANSMIT=0
        SET_LED LED=my_neopixel RED=0.0 GREEN=0.0 BLUE=0.5 INDEX=4 TRANSMIT=0
        SET_LED LED=my_neopixel RED=0.0 GREEN=0.0 BLUE=0.5 INDEX=5 TRANSMIT=0
        SET_LED LED=my_neopixel RED=0.0 GREEN=0.0 BLUE=0.5 INDEX=6 TRANSMIT=0
        SET_LED LED=my_neopixel RED=0.0 GREEN=0.0 BLUE=0.5 INDEX=7 TRANSMIT=0
        SET_LED LED=my_neopixel RED=0.0 GREEN=0.0 BLUE=0.5 INDEX=8 TRANSMIT=0
        SET_LED LED=my_neopixel RED=0.0 GREEN=0.0 BLUE=0.5 INDEX=9 TRANSMIT=0
        SET_LED LED=my_neopixel RED=0.0 GREEN=0.5 BLUE=0.0 INDEX=10 TRANSMIT=0
        SET_LED LED=my_neopixel RED=0.0 GREEN=0.5 BLUE=0.0 INDEX=11 TRANSMIT=0
        SET_LED LED=my_neopixel RED=0.0 GREEN=0.5 BLUE=0.0 INDEX=12 TRANSMIT=0
        SET_LED LED=my_neopixel RED=0.0 GREEN=0.5 BLUE=0.0 INDEX=13 TRANSMIT=0
        SET_LED LED=my_neopixel RED=0.0 GREEN=0.5 BLUE=0.0 INDEX=14 TRANSMIT=0
        SET_LED LED=my_neopixel RED=0.0 GREEN=0.5 BLUE=0.0 INDEX=15 TRANSMIT=0
        SET_LED LED=my_neopixel RED=0.0 GREEN=0.5 BLUE=0.0 INDEX=16 TRANSMIT=0
        SET_LED LED=my_neopixel RED=0.0 GREEN=0.5 BLUE=0.0 INDEX=17 TRANSMIT=0
        SET_LED LED=my_neopixel RED=0.0 GREEN=0.5 BLUE=0.0 INDEX=18 TRANSMIT=0
        SET_LED LED=my_neopixel RED=0.5 GREEN=0.0 BLUE=0.0 INDEX=19 TRANSMIT=0
        SET_LED LED=my_neopixel RED=0.5 GREEN=0.0 BLUE=0.0 INDEX=20 TRANSMIT=0
        SET_LED LED=my_neopixel RED=0.5 GREEN=0.0 BLUE=0.0 INDEX=21 TRANSMIT=0
        SET_LED LED=my_neopixel RED=0.5 GREEN=0.0 BLUE=0.0 INDEX=22 TRANSMIT=0
        SET_LED LED=my_neopixel RED=0.5 GREEN=0.0 BLUE=0.0 INDEX=23 TRANSMIT=0
        SET_LED LED=my_neopixel RED=0.5 GREEN=0.0 BLUE=0.0 INDEX=24 TRANSMIT=0
        SET_LED LED=my_neopixel RED=0.5 GREEN=0.0 BLUE=0.0 INDEX=25 TRANSMIT=0
        SET_LED LED=my_neopixel RED=0.5 GREEN=0.0 BLUE=0.0 INDEX=26 TRANSMIT=0
        SET_LED LED=my_neopixel RED=0.5 GREEN=0.0 BLUE=0.0 INDEX=27 TRANSMIT=1
	G4 P250                       ; пауза 250ms
        SET_LED LED=my_neopixel RED=0.5 GREEN=0.0 BLUE=0.0 INDEX=1 TRANSMIT=0
        SET_LED LED=my_neopixel RED=0.5 GREEN=0.0 BLUE=0.0 INDEX=2 TRANSMIT=0
        SET_LED LED=my_neopixel RED=0.5 GREEN=0.0 BLUE=0.0 INDEX=3 TRANSMIT=0
        SET_LED LED=my_neopixel RED=0.5 GREEN=0.0 BLUE=0.0 INDEX=4 TRANSMIT=0
        SET_LED LED=my_neopixel RED=0.5 GREEN=0.0 BLUE=0.0 INDEX=5 TRANSMIT=0
        SET_LED LED=my_neopixel RED=0.5 GREEN=0.0 BLUE=0.0 INDEX=6 TRANSMIT=0
        SET_LED LED=my_neopixel RED=0.5 GREEN=0.0 BLUE=0.0 INDEX=7 TRANSMIT=0
        SET_LED LED=my_neopixel RED=0.5 GREEN=0.0 BLUE=0.0 INDEX=8 TRANSMIT=0
        SET_LED LED=my_neopixel RED=0.5 GREEN=0.0 BLUE=0.0 INDEX=9 TRANSMIT=0
        SET_LED LED=my_neopixel RED=0.0 GREEN=0.0 BLUE=0.5 INDEX=10 TRANSMIT=0
        SET_LED LED=my_neopixel RED=0.0 GREEN=0.0 BLUE=0.5 INDEX=11 TRANSMIT=0
        SET_LED LED=my_neopixel RED=0.0 GREEN=0.0 BLUE=0.5 INDEX=12 TRANSMIT=0
        SET_LED LED=my_neopixel RED=0.0 GREEN=0.0 BLUE=0.5 INDEX=13 TRANSMIT=0
        SET_LED LED=my_neopixel RED=0.0 GREEN=0.0 BLUE=0.5 INDEX=14 TRANSMIT=0
        SET_LED LED=my_neopixel RED=0.0 GREEN=0.0 BLUE=0.5 INDEX=15 TRANSMIT=0
        SET_LED LED=my_neopixel RED=0.0 GREEN=0.0 BLUE=0.5 INDEX=16 TRANSMIT=0
        SET_LED LED=my_neopixel RED=0.0 GREEN=0.0 BLUE=0.5 INDEX=17 TRANSMIT=0
        SET_LED LED=my_neopixel RED=0.0 GREEN=0.0 BLUE=0.5 INDEX=18 TRANSMIT=0
        SET_LED LED=my_neopixel RED=0.0 GREEN=0.5 BLUE=0.0 INDEX=19 TRANSMIT=0
        SET_LED LED=my_neopixel RED=0.0 GREEN=0.5 BLUE=0.0 INDEX=20 TRANSMIT=0
        SET_LED LED=my_neopixel RED=0.0 GREEN=0.5 BLUE=0.0 INDEX=21 TRANSMIT=0
        SET_LED LED=my_neopixel RED=0.0 GREEN=0.5 BLUE=0.0 INDEX=22 TRANSMIT=0
        SET_LED LED=my_neopixel RED=0.0 GREEN=0.5 BLUE=0.0 INDEX=23 TRANSMIT=0
        SET_LED LED=my_neopixel RED=0.0 GREEN=0.5 BLUE=0.0 INDEX=24 TRANSMIT=0
        SET_LED LED=my_neopixel RED=0.0 GREEN=0.5 BLUE=0.0 INDEX=25 TRANSMIT=0
        SET_LED LED=my_neopixel RED=0.0 GREEN=0.5 BLUE=0.0 INDEX=26 TRANSMIT=0
        SET_LED LED=my_neopixel RED=0.0 GREEN=0.5 BLUE=0.0 INDEX=27 TRANSMIT=1
      
	G4 P250                       ; пауза 250ms
        SET_LED LED=my_neopixel RED=0.0 GREEN=0.5 BLUE=0.0 INDEX=1 TRANSMIT=0
        SET_LED LED=my_neopixel RED=0.0 GREEN=0.5 BLUE=0.0 INDEX=2 TRANSMIT=0
        SET_LED LED=my_neopixel RED=0.0 GREEN=0.5 BLUE=0.0 INDEX=3 TRANSMIT=0
        SET_LED LED=my_neopixel RED=0.0 GREEN=0.5 BLUE=0.0 INDEX=4 TRANSMIT=0
        SET_LED LED=my_neopixel RED=0.0 GREEN=0.5 BLUE=0.0 INDEX=5 TRANSMIT=0
        SET_LED LED=my_neopixel RED=0.0 GREEN=0.5 BLUE=0.0 INDEX=6 TRANSMIT=0
        SET_LED LED=my_neopixel RED=0.0 GREEN=0.5 BLUE=0.0 INDEX=7 TRANSMIT=0
        SET_LED LED=my_neopixel RED=0.0 GREEN=0.5 BLUE=0.0 INDEX=8 TRANSMIT=0
        SET_LED LED=my_neopixel RED=0.0 GREEN=0.5 BLUE=0.0 INDEX=9 TRANSMIT=0
        SET_LED LED=my_neopixel RED=0.5 GREEN=0.0 BLUE=0.0 INDEX=10 TRANSMIT=0
        SET_LED LED=my_neopixel RED=0.5 GREEN=0.0 BLUE=0.0 INDEX=11 TRANSMIT=0
        SET_LED LED=my_neopixel RED=0.5 GREEN=0.0 BLUE=0.0 INDEX=12 TRANSMIT=0
        SET_LED LED=my_neopixel RED=0.5 GREEN=0.0 BLUE=0.0 INDEX=13 TRANSMIT=0
        SET_LED LED=my_neopixel RED=0.5 GREEN=0.0 BLUE=0.0 INDEX=14 TRANSMIT=0
        SET_LED LED=my_neopixel RED=0.5 GREEN=0.0 BLUE=0.0 INDEX=15 TRANSMIT=0
        SET_LED LED=my_neopixel RED=0.5 GREEN=0.0 BLUE=0.0 INDEX=16 TRANSMIT=0
        SET_LED LED=my_neopixel RED=0.5 GREEN=0.0 BLUE=0.0 INDEX=17 TRANSMIT=0
        SET_LED LED=my_neopixel RED=0.5 GREEN=0.0 BLUE=0.0 INDEX=18 TRANSMIT=0
        SET_LED LED=my_neopixel RED=0.0 GREEN=0.0 BLUE=0.5 INDEX=19 TRANSMIT=0
        SET_LED LED=my_neopixel RED=0.0 GREEN=0.0 BLUE=0.5 INDEX=20 TRANSMIT=0
        SET_LED LED=my_neopixel RED=0.0 GREEN=0.0 BLUE=0.5 INDEX=21 TRANSMIT=0
        SET_LED LED=my_neopixel RED=0.0 GREEN=0.0 BLUE=0.5 INDEX=22 TRANSMIT=0
        SET_LED LED=my_neopixel RED=0.0 GREEN=0.0 BLUE=0.5 INDEX=23 TRANSMIT=0
        SET_LED LED=my_neopixel RED=0.0 GREEN=0.0 BLUE=0.5 INDEX=24 TRANSMIT=0
        SET_LED LED=my_neopixel RED=0.0 GREEN=0.0 BLUE=0.5 INDEX=25 TRANSMIT=0
        SET_LED LED=my_neopixel RED=0.0 GREEN=0.0 BLUE=0.5 INDEX=26 TRANSMIT=0
        SET_LED LED=my_neopixel RED=0.0 GREEN=0.0 BLUE=0.5 INDEX=27 TRANSMIT=1

	G4 P250                       ; пауза 250ms
        SET_LED LED=my_neopixel RED=0.0 GREEN=0.5 BLUE=0.0 INDEX=1 TRANSMIT=0
        SET_LED LED=my_neopixel RED=0.0 GREEN=0.5 BLUE=0.0 INDEX=2 TRANSMIT=0
        SET_LED LED=my_neopixel RED=0.0 GREEN=0.5 BLUE=0.0 INDEX=3 TRANSMIT=0
        SET_LED LED=my_neopixel RED=0.0 GREEN=0.0 BLUE=0.5 INDEX=4 TRANSMIT=0
        SET_LED LED=my_neopixel RED=0.0 GREEN=0.0 BLUE=0.5 INDEX=5 TRANSMIT=0
        SET_LED LED=my_neopixel RED=0.0 GREEN=0.0 BLUE=0.5 INDEX=6 TRANSMIT=0
        SET_LED LED=my_neopixel RED=0.0 GREEN=0.5 BLUE=0.0 INDEX=7 TRANSMIT=0
        SET_LED LED=my_neopixel RED=0.0 GREEN=0.5 BLUE=0.0 INDEX=8 TRANSMIT=0
        SET_LED LED=my_neopixel RED=0.0 GREEN=0.5 BLUE=0.0 INDEX=9 TRANSMIT=0
        SET_LED LED=my_neopixel RED=0.5 GREEN=0.0 BLUE=0.0 INDEX=10 TRANSMIT=0
        SET_LED LED=my_neopixel RED=0.5 GREEN=0.0 BLUE=0.0 INDEX=11 TRANSMIT=0
        SET_LED LED=my_neopixel RED=0.5 GREEN=0.0 BLUE=0.0 INDEX=12 TRANSMIT=0
        SET_LED LED=my_neopixel RED=0.0 GREEN=0.5 BLUE=0.0 INDEX=13 TRANSMIT=0
        SET_LED LED=my_neopixel RED=0.0 GREEN=0.5 BLUE=0.0 INDEX=14 TRANSMIT=0
        SET_LED LED=my_neopixel RED=0.0 GREEN=0.5 BLUE=0.0 INDEX=15 TRANSMIT=0
        SET_LED LED=my_neopixel RED=0.5 GREEN=0.0 BLUE=0.0 INDEX=16 TRANSMIT=0
        SET_LED LED=my_neopixel RED=0.5 GREEN=0.0 BLUE=0.0 INDEX=17 TRANSMIT=0
        SET_LED LED=my_neopixel RED=0.5 GREEN=0.0 BLUE=0.0 INDEX=18 TRANSMIT=0
        SET_LED LED=my_neopixel RED=0.0 GREEN=0.0 BLUE=0.5 INDEX=19 TRANSMIT=0
        SET_LED LED=my_neopixel RED=0.0 GREEN=0.0 BLUE=0.5 INDEX=20 TRANSMIT=0
        SET_LED LED=my_neopixel RED=0.0 GREEN=0.0 BLUE=0.5 INDEX=21 TRANSMIT=0
        SET_LED LED=my_neopixel RED=0.5 GREEN=0.0 BLUE=0.0 INDEX=22 TRANSMIT=0
        SET_LED LED=my_neopixel RED=0.5 GREEN=0.0 BLUE=0.0 INDEX=23 TRANSMIT=0
        SET_LED LED=my_neopixel RED=0.5 GREEN=0.0 BLUE=0.0 INDEX=24 TRANSMIT=0
        SET_LED LED=my_neopixel RED=0.0 GREEN=0.0 BLUE=0.5 INDEX=25 TRANSMIT=0
        SET_LED LED=my_neopixel RED=0.0 GREEN=0.0 BLUE=0.5 INDEX=26 TRANSMIT=0
        SET_LED LED=my_neopixel RED=0.0 GREEN=0.0 BLUE=0.5 INDEX=27 TRANSMIT=1

	G4 P250                       ; пауза 250ms
    {% endfor %}
    SET_LED LED=my_neopixel RED=0.3 GREEN=0.3 BLUE=0.3
```
второй макрос попроще. 

он включит первый макрос через пять секунд после включения принтера. 

```g-code
[delayed_gcode welcome]
initial_duration: 5. #тут можно вписать другое количество секунд (главное - точку не удаляйте)
gcode:
   PartyTime
```

**что получилось в итоге**

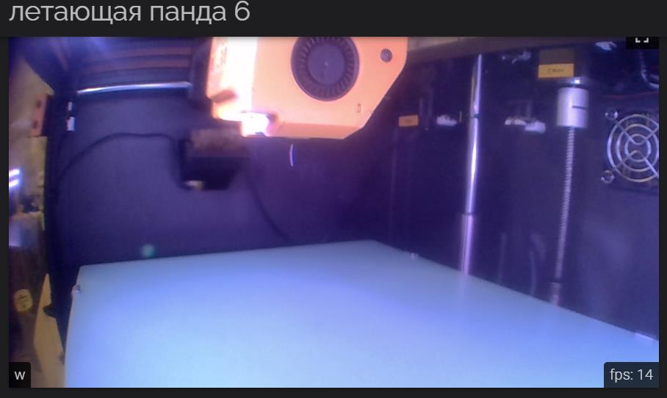
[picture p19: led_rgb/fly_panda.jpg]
вид
 
 
 видео

ну и еще макрос бонусом. полицейская сирена, сделана на 12 светодиодов но никто не мешает расширить на ваше количество
```g-code
[gcode_macro POLICE_Time]
gcode:
    {% for flashes in range(params.COUNT|default(20)|int) %}
        SET_LED LED=my_neopixel RED=1.0 GREEN=0.0 BLUE=0.0 INDEX=1 TRANSMIT=0
        SET_LED LED=my_neopixel RED=1.0 GREEN=0.0 BLUE=0.0 INDEX=2 TRANSMIT=0
        SET_LED LED=my_neopixel RED=1.0 GREEN=0.0 BLUE=0.0 INDEX=3 TRANSMIT=0
        SET_LED LED=my_neopixel RED=1.0 GREEN=0.0 BLUE=0.0 INDEX=4 TRANSMIT=0
        SET_LED LED=my_neopixel RED=1.0 GREEN=0.0 BLUE=0.0 INDEX=5 TRANSMIT=0
        SET_LED LED=my_neopixel RED=0.3 GREEN=0.3 BLUE=0.3 INDEX=6 TRANSMIT=0
        SET_LED LED=my_neopixel RED=0.3 GREEN=0.3 BLUE=0.3 INDEX=7 TRANSMIT=0
        SET_LED LED=my_neopixel RED=0.0 GREEN=0.0 BLUE=0.0 INDEX=8 TRANSMIT=0
        SET_LED LED=my_neopixel RED=0.0 GREEN=0.0 BLUE=0.0 INDEX=9 TRANSMIT=0
        SET_LED LED=my_neopixel RED=0.0 GREEN=0.0 BLUE=0.0 INDEX=10 TRANSMIT=0
        SET_LED LED=my_neopixel RED=0.0 GREEN=0.0 BLUE=0.0 INDEX=11 TRANSMIT=0
        SET_LED LED=my_neopixel RED=0.0 GREEN=0.0 BLUE=0.0 INDEX=12 TRANSMIT=1
    
        G4 P150                       ; sleep 150ms   
        SET_LED LED=my_neopixel RED=0.0 GREEN=0.0 BLUE=0.0 INDEX=1 TRANSMIT=0
        SET_LED LED=my_neopixel RED=0.0 GREEN=0.0 BLUE=0.0 INDEX=2 TRANSMIT=0
        SET_LED LED=my_neopixel RED=0.0 GREEN=0.0 BLUE=0.0 INDEX=3 TRANSMIT=0
        SET_LED LED=my_neopixel RED=0.0 GREEN=0.0 BLUE=0.0 INDEX=4 TRANSMIT=0
        SET_LED LED=my_neopixel RED=0.0 GREEN=0.0 BLUE=0.0 INDEX=5 TRANSMIT=0
        SET_LED LED=my_neopixel RED=0.3 GREEN=0.3 BLUE=0.3 INDEX=6 TRANSMIT=0
        SET_LED LED=my_neopixel RED=0.3 GREEN=0.3 BLUE=0.3 INDEX=7 TRANSMIT=0
        SET_LED LED=my_neopixel RED=0.0 GREEN=0.0 BLUE=0.0 INDEX=8 TRANSMIT=0
        SET_LED LED=my_neopixel RED=0.0 GREEN=0.0 BLUE=0.0 INDEX=9 TRANSMIT=0
        SET_LED LED=my_neopixel RED=0.0 GREEN=0.0 BLUE=0.0 INDEX=10 TRANSMIT=0
        SET_LED LED=my_neopixel RED=0.0 GREEN=0.0 BLUE=0.0 INDEX=11 TRANSMIT=0
        SET_LED LED=my_neopixel RED=0.0 GREEN=0.0 BLUE=0.0 INDEX=12 TRANSMIT=1
    
        G4 P150                       ; sleep 150ms   
        SET_LED LED=my_neopixel RED=1.0 GREEN=0.0 BLUE=0.0 INDEX=1 TRANSMIT=0
        SET_LED LED=my_neopixel RED=1.0 GREEN=0.0 BLUE=0.0 INDEX=2 TRANSMIT=0
        SET_LED LED=my_neopixel RED=1.0 GREEN=0.0 BLUE=0.0 INDEX=3 TRANSMIT=0
        SET_LED LED=my_neopixel RED=1.0 GREEN=0.0 BLUE=0.0 INDEX=4 TRANSMIT=0
        SET_LED LED=my_neopixel RED=1.0 GREEN=0.0 BLUE=0.0 INDEX=5 TRANSMIT=0
        SET_LED LED=my_neopixel RED=0.3 GREEN=0.3 BLUE=0.3 INDEX=6 TRANSMIT=0
        SET_LED LED=my_neopixel RED=0.3 GREEN=0.3 BLUE=0.3 INDEX=7 TRANSMIT=0
        SET_LED LED=my_neopixel RED=0.0 GREEN=0.0 BLUE=0.0 INDEX=8 TRANSMIT=0
        SET_LED LED=my_neopixel RED=0.0 GREEN=0.0 BLUE=0.0 INDEX=9 TRANSMIT=0
        SET_LED LED=my_neopixel RED=0.0 GREEN=0.0 BLUE=0.0 INDEX=10 TRANSMIT=0
        SET_LED LED=my_neopixel RED=0.0 GREEN=0.0 BLUE=0.0 INDEX=11 TRANSMIT=0
        SET_LED LED=my_neopixel RED=0.0 GREEN=0.0 BLUE=0.0 INDEX=12 TRANSMIT=1
    
        G4 P150                       ; sleep 150ms  
        SET_LED LED=my_neopixel RED=0.0 GREEN=0.0 BLUE=0.0 INDEX=1 TRANSMIT=0
        SET_LED LED=my_neopixel RED=0.0 GREEN=0.0 BLUE=0.0 INDEX=2 TRANSMIT=0
        SET_LED LED=my_neopixel RED=0.0 GREEN=0.0 BLUE=0.0 INDEX=3 TRANSMIT=0
        SET_LED LED=my_neopixel RED=0.0 GREEN=0.0 BLUE=0.0 INDEX=4 TRANSMIT=0
        SET_LED LED=my_neopixel RED=0.0 GREEN=0.0 BLUE=0.0 INDEX=5 TRANSMIT=0
        SET_LED LED=my_neopixel RED=0.3 GREEN=0.3 BLUE=0.3 INDEX=6 TRANSMIT=0
        SET_LED LED=my_neopixel RED=0.3 GREEN=0.3 BLUE=0.3 INDEX=7 TRANSMIT=0
        SET_LED LED=my_neopixel RED=0.0 GREEN=0.0 BLUE=0.0 INDEX=8 TRANSMIT=0
        SET_LED LED=my_neopixel RED=0.0 GREEN=0.0 BLUE=0.0 INDEX=9 TRANSMIT=0
        SET_LED LED=my_neopixel RED=0.0 GREEN=0.0 BLUE=0.0 INDEX=10 TRANSMIT=0
        SET_LED LED=my_neopixel RED=0.0 GREEN=0.0 BLUE=0.0 INDEX=11 TRANSMIT=0
        SET_LED LED=my_neopixel RED=0.0 GREEN=0.0 BLUE=0.0 INDEX=12 TRANSMIT=1

        G4 P150                       ; sleep 150ms   
        SET_LED LED=my_neopixel RED=1.0 GREEN=0.0 BLUE=0.0 INDEX=1 TRANSMIT=0
        SET_LED LED=my_neopixel RED=1.0 GREEN=0.0 BLUE=0.0 INDEX=2 TRANSMIT=0
        SET_LED LED=my_neopixel RED=1.0 GREEN=0.0 BLUE=0.0 INDEX=3 TRANSMIT=0
        SET_LED LED=my_neopixel RED=1.0 GREEN=0.0 BLUE=0.0 INDEX=4 TRANSMIT=0
        SET_LED LED=my_neopixel RED=1.0 GREEN=0.0 BLUE=0.0 INDEX=5 TRANSMIT=0
        SET_LED LED=my_neopixel RED=0.3 GREEN=0.3 BLUE=0.3 INDEX=6 TRANSMIT=0
        SET_LED LED=my_neopixel RED=0.3 GREEN=0.3 BLUE=0.3 INDEX=7 TRANSMIT=0
        SET_LED LED=my_neopixel RED=0.0 GREEN=0.0 BLUE=0.0 INDEX=8 TRANSMIT=0
        SET_LED LED=my_neopixel RED=0.0 GREEN=0.0 BLUE=0.0 INDEX=9 TRANSMIT=0
        SET_LED LED=my_neopixel RED=0.0 GREEN=0.0 BLUE=0.0 INDEX=10 TRANSMIT=0
        SET_LED LED=my_neopixel RED=0.0 GREEN=0.0 BLUE=0.0 INDEX=11 TRANSMIT=0
        SET_LED LED=my_neopixel RED=0.0 GREEN=0.0 BLUE=0.0 INDEX=12 TRANSMIT=1

        G4 P150                       ; sleep 150ms  
        SET_LED LED=my_neopixel RED=0.0 GREEN=0.0 BLUE=0.0 INDEX=1 TRANSMIT=0
        SET_LED LED=my_neopixel RED=0.0 GREEN=0.0 BLUE=0.0 INDEX=2 TRANSMIT=0
        SET_LED LED=my_neopixel RED=0.0 GREEN=0.0 BLUE=0.0 INDEX=3 TRANSMIT=0
        SET_LED LED=my_neopixel RED=0.0 GREEN=0.0 BLUE=0.0 INDEX=4 TRANSMIT=0
        SET_LED LED=my_neopixel RED=0.0 GREEN=0.0 BLUE=0.0 INDEX=5 TRANSMIT=0
        SET_LED LED=my_neopixel RED=0.3 GREEN=0.3 BLUE=0.3 INDEX=6 TRANSMIT=0
        SET_LED LED=my_neopixel RED=0.3 GREEN=0.3 BLUE=0.3 INDEX=7 TRANSMIT=0
        SET_LED LED=my_neopixel RED=0.0 GREEN=0.0 BLUE=1.0 INDEX=8 TRANSMIT=0
        SET_LED LED=my_neopixel RED=0.0 GREEN=0.0 BLUE=1.0 INDEX=9 TRANSMIT=0
        SET_LED LED=my_neopixel RED=0.0 GREEN=0.0 BLUE=1.0 INDEX=10 TRANSMIT=0
        SET_LED LED=my_neopixel RED=0.0 GREEN=0.0 BLUE=1.0 INDEX=11 TRANSMIT=0
        SET_LED LED=my_neopixel RED=0.0 GREEN=0.0 BLUE=1.0 INDEX=12 TRANSMIT=1

        G4 P150                       ; sleep 150ms  
        SET_LED LED=my_neopixel RED=0.0 GREEN=0.0 BLUE=0.0 INDEX=1 TRANSMIT=0
        SET_LED LED=my_neopixel RED=0.0 GREEN=0.0 BLUE=0.0 INDEX=2 TRANSMIT=0
        SET_LED LED=my_neopixel RED=0.0 GREEN=0.0 BLUE=0.0 INDEX=3 TRANSMIT=0
        SET_LED LED=my_neopixel RED=0.0 GREEN=0.0 BLUE=0.0 INDEX=4 TRANSMIT=0
        SET_LED LED=my_neopixel RED=0.0 GREEN=0.0 BLUE=0.0 INDEX=5 TRANSMIT=0
        SET_LED LED=my_neopixel RED=0.3 GREEN=0.3 BLUE=0.3 INDEX=6 TRANSMIT=0
        SET_LED LED=my_neopixel RED=0.3 GREEN=0.3 BLUE=0.3 INDEX=7 TRANSMIT=0
        SET_LED LED=my_neopixel RED=0.0 GREEN=0.0 BLUE=0.0 INDEX=8 TRANSMIT=0
        SET_LED LED=my_neopixel RED=0.0 GREEN=0.0 BLUE=0.0 INDEX=9 TRANSMIT=0
        SET_LED LED=my_neopixel RED=0.0 GREEN=0.0 BLUE=0.0 INDEX=10 TRANSMIT=0
        SET_LED LED=my_neopixel RED=0.0 GREEN=0.0 BLUE=0.0 INDEX=11 TRANSMIT=0
        SET_LED LED=my_neopixel RED=0.0 GREEN=0.0 BLUE=0.0 INDEX=12 TRANSMIT=1

        G4 P150                       ; sleep 150ms  
        SET_LED LED=my_neopixel RED=0.0 GREEN=0.0 BLUE=0.0 INDEX=1 TRANSMIT=0
        SET_LED LED=my_neopixel RED=0.0 GREEN=0.0 BLUE=0.0 INDEX=2 TRANSMIT=0
        SET_LED LED=my_neopixel RED=0.0 GREEN=0.0 BLUE=0.0 INDEX=3 TRANSMIT=0
        SET_LED LED=my_neopixel RED=0.0 GREEN=0.0 BLUE=0.0 INDEX=4 TRANSMIT=0
        SET_LED LED=my_neopixel RED=0.0 GREEN=0.0 BLUE=0.0 INDEX=5 TRANSMIT=0
        SET_LED LED=my_neopixel RED=0.3 GREEN=0.3 BLUE=0.3 INDEX=6 TRANSMIT=0
        SET_LED LED=my_neopixel RED=0.3 GREEN=0.3 BLUE=0.3 INDEX=7 TRANSMIT=0
        SET_LED LED=my_neopixel RED=0.0 GREEN=0.0 BLUE=1.0 INDEX=8 TRANSMIT=0
        SET_LED LED=my_neopixel RED=0.0 GREEN=0.0 BLUE=1.0 INDEX=9 TRANSMIT=0
        SET_LED LED=my_neopixel RED=0.0 GREEN=0.0 BLUE=1.0 INDEX=10 TRANSMIT=0
        SET_LED LED=my_neopixel RED=0.0 GREEN=0.0 BLUE=1.0 INDEX=11 TRANSMIT=0
        SET_LED LED=my_neopixel RED=0.0 GREEN=0.0 BLUE=1.0 INDEX=12 TRANSMIT=1

        G4 P150                       ; sleep 150ms  
        SET_LED LED=my_neopixel RED=0.0 GREEN=0.0 BLUE=0.0 INDEX=1 TRANSMIT=0
        SET_LED LED=my_neopixel RED=0.0 GREEN=0.0 BLUE=0.0 INDEX=2 TRANSMIT=0
        SET_LED LED=my_neopixel RED=0.0 GREEN=0.0 BLUE=0.0 INDEX=3 TRANSMIT=0
        SET_LED LED=my_neopixel RED=0.0 GREEN=0.0 BLUE=0.0 INDEX=4 TRANSMIT=0
        SET_LED LED=my_neopixel RED=0.0 GREEN=0.0 BLUE=0.0 INDEX=5 TRANSMIT=0
        SET_LED LED=my_neopixel RED=0.3 GREEN=0.3 BLUE=0.3 INDEX=6 TRANSMIT=0
        SET_LED LED=my_neopixel RED=0.3 GREEN=0.3 BLUE=0.3 INDEX=7 TRANSMIT=0
        SET_LED LED=my_neopixel RED=0.0 GREEN=0.0 BLUE=0.0 INDEX=8 TRANSMIT=0
        SET_LED LED=my_neopixel RED=0.0 GREEN=0.0 BLUE=0.0 INDEX=9 TRANSMIT=0
        SET_LED LED=my_neopixel RED=0.0 GREEN=0.0 BLUE=0.0 INDEX=10 TRANSMIT=0
        SET_LED LED=my_neopixel RED=0.0 GREEN=0.0 BLUE=0.0 INDEX=11 TRANSMIT=0
        SET_LED LED=my_neopixel RED=0.0 GREEN=0.0 BLUE=0.0 INDEX=12 TRANSMIT=1

        G4 P150                       ; sleep 150ms  
        SET_LED LED=my_neopixel RED=0.0 GREEN=0.0 BLUE=0.0 INDEX=1 TRANSMIT=0
        SET_LED LED=my_neopixel RED=0.0 GREEN=0.0 BLUE=0.0 INDEX=2 TRANSMIT=0
        SET_LED LED=my_neopixel RED=0.0 GREEN=0.0 BLUE=0.0 INDEX=3 TRANSMIT=0
        SET_LED LED=my_neopixel RED=0.0 GREEN=0.0 BLUE=0.0 INDEX=4 TRANSMIT=0
        SET_LED LED=my_neopixel RED=0.0 GREEN=0.0 BLUE=0.0 INDEX=5 TRANSMIT=0
        SET_LED LED=my_neopixel RED=0.3 GREEN=0.3 BLUE=0.3 INDEX=6 TRANSMIT=0
        SET_LED LED=my_neopixel RED=0.3 GREEN=0.3 BLUE=0.3 INDEX=7 TRANSMIT=0
        SET_LED LED=my_neopixel RED=0.0 GREEN=0.0 BLUE=1.0 INDEX=8 TRANSMIT=0
        SET_LED LED=my_neopixel RED=0.0 GREEN=0.0 BLUE=1.0 INDEX=9 TRANSMIT=0
        SET_LED LED=my_neopixel RED=0.0 GREEN=0.0 BLUE=1.0 INDEX=10 TRANSMIT=0
        SET_LED LED=my_neopixel RED=0.0 GREEN=0.0 BLUE=1.0 INDEX=11 TRANSMIT=0
        SET_LED LED=my_neopixel RED=0.0 GREEN=0.0 BLUE=1.0 INDEX=12 TRANSMIT=1

        G4 P150                       ; sleep 150ms
     {% endfor %} 
       SET_LED LED=my_neopixel RED=0.5 GREEN=0.5 BLUE=0.5
```

Для тех кто домотал до самого низу [бонус](https://github.com/digitalninja-ro/klipper-neopixel) Это ссылка на ресурс с макросами прогрессбара и индикации температуры хотенда и вот ссылка на [видео](https://youtu.be/14LC8Tcd_JQ) c ними.

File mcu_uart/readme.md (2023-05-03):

<h3 align="right"><a href="https://pay.cloudtips.ru/p/f84bf0b2" target="_blank">ваше "спасибо" автору </a> </h3>

**Подключение принтера по UART**

[versión en español](esp_readme.md)

Главная путаница возникает у пользователей в наименовании номер UART, запоминаем простое правило: в printer.cfg мы указываем номер UART на одноплатнике, при компиляции прошивки в menu config мы пишем номер UART платы принтера.

подключаем как указано на фото.

```bash
sudo armbian-config
```
 раздел system подраздел hardware-  включаем uart3 

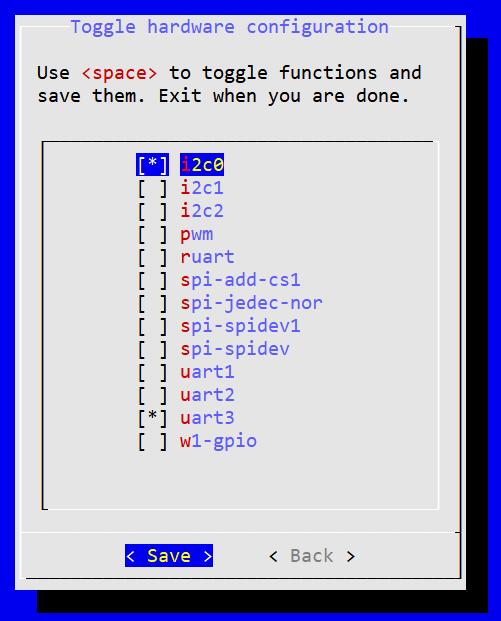
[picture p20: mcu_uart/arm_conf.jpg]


переделываем прошивку для uart подключения

```bash
cd ~/klipper
make clean
make menuconfig
```
Micro-Controller architecture - выбираем STM32

Processor model - выбираем STM32F407

Bootloader offset - 48KiB bootloader

Comunication Interface - Serial (on USART1 PA10/PA9)

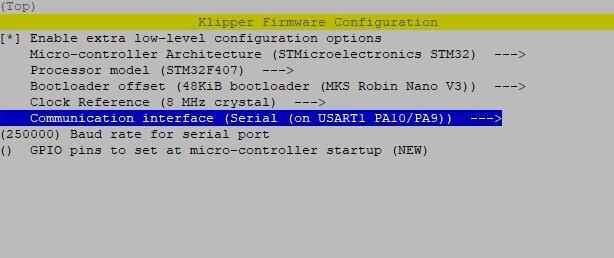
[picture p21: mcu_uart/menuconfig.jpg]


Нажимаем Q, сохраняя внесенные изменения и компилируем прошивку:

```bash
make
```
прошивка скомпилировалась и находится в папке ~/klipper/out/klipper.bin 
забираем и переименовываем в Robin_nano_4.bin закидываем на карту и включаем принтер. Прошивка занимает около минуты. если прошивка удачная то на карте у вас окажется файл Robin_nano_4.cur
OrangePi 3 LTS для UART подключения использует оверлей uart3 и устройство /dev/ttyS3

В printer.cfg  ищем раздел mcu и меняем на такой вид
```bash
[mcu]
serial: /dev/ttyS3
restart_method: command
```
ниже расположены картинки как\куда именно втыкать провода в разъем WIFI и пишку.
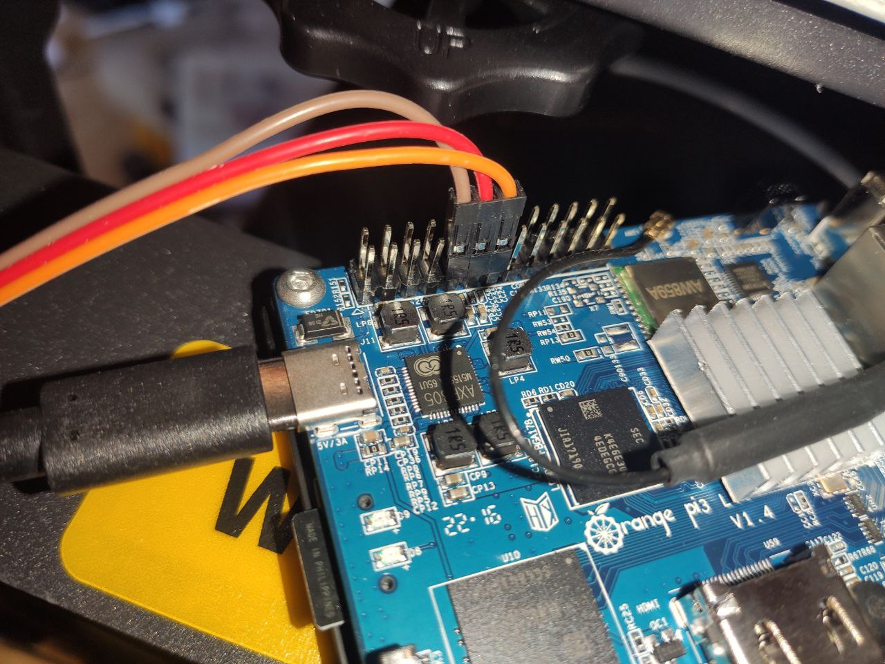
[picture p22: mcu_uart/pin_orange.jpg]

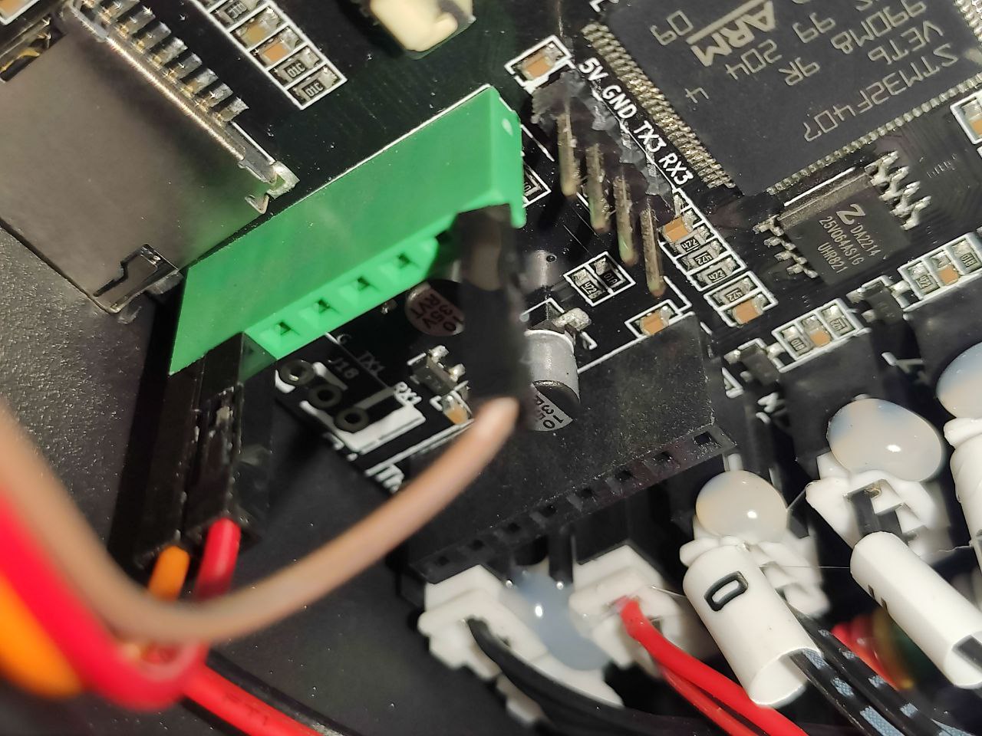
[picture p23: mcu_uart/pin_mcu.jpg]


общий вид платы:

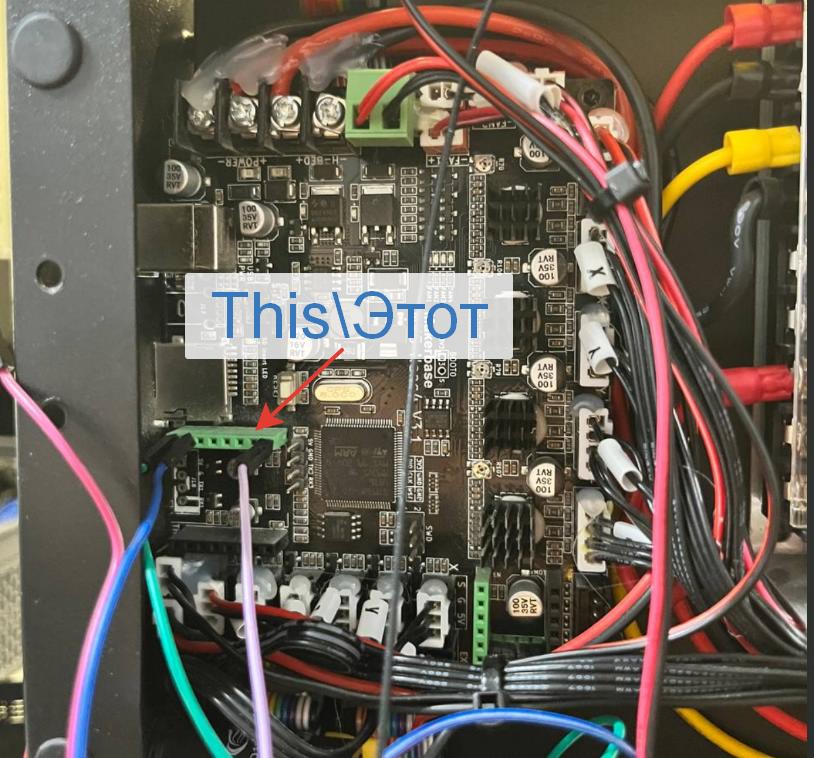
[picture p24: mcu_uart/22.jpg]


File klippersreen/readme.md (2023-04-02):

**Установка klippersreen** 

*Выжимка из чата обсуждения установки* 

На самом деле после установки через `kiah` должно само заработать сразу, решение с тачскрином ниже.

В `/etc/X11/Xwrapper.config` нужно добавить:
```bash
allowed_users=anybody
needs_root_rights=yes
```
Замена драйвера:
```bash
sudo systemctl stop KlipperScreen.service
sudo mv /etc/X11/xorg.conf.d/50-fbturbo.conf /etc/X11/xorg.conf.d/50-fbdev.conf
sudo apt-get remove xserver-xorg-video-fbturbo
sudo apt-get install xserver-xorg-video-fbdev
```
В файле `/etc/X11/xorg.conf.d/50-fbdev.conf` изменить Driver на fbdev:
```bash
Section "Device"
        Identifier      "Allwinner FBDEV"
        Driver          "fbdev"
        Option          "fbdev" "/dev/fb0"
        Option          "SwapbuffersWait" "true"
EndSection
```
Установить пакет `xserver-xorg-input-libinput`:
```bash
sudo apt install xserver-xorg-input-libinput
```
В armbian конфиге: `sudo nano /boot/armbianEnv.txt` прописать стройки касаемо HDMI:
- 5 дюймов
```bash
max_usb_current=1
hdmi_force_hotplug=1
config_hdmi_boost=7
hdmi_group=2
hdmi_mode=87
hdmi_drive=2
hdmi_cvt 800 480 60 6 0 0 0
```
- 7 дюймов:
```bash
max_usb_current=1
hdmi_force_hotplug=1
config_hdmi_boost=10
hdmi_group=2
hdmi_mode=87
hdmi_ctv 1024 600 60 6 0 0 0
```
Еще прописал в файле `/usr/share/X11/xorg.conf.d/90-monitor.conf` такое:
```bash
Section "Monitor"
    Identifier "HDMI-1"
    # This identifier would be the same as the name of the connector printed by xrandr.
    # it can be "HDMI-0" "DisplayPort-0", "DSI-0", "DVI-0", "DPI-0" etc
    Option "Rotate" "normal"
    # Valid rotation options are normal,inverted,left,right
    Option "PreferredMode" "800x480"
    # May be necesary if you are not getting your prefered resolution.
EndSection
```
Ну я бы сказал что это скорее всего является извращенной инструкцией и ставить клипперскрин лучше вручную, через это:
```bash
cd ~/
git clone https://github.com/jordanruthe/KlipperScreen.git
cd ~/KlipperScreen
./scripts/KlipperScreen-install.sh
```
Потом сюда moonraker.conf добавить это:
```gcode
[authorization]
trusted_clients:
  127.0.0.1
```
Если там уже есть адреса, то просто дописать его.

**Настраиваем тач:**

1. нашел еще руководство по экранам http://www.lcdwiki.com/7inch_HDMI_Display-C возможно после прочтения остальное будет не нужно.

2.Данная строка сразу меняет расположение и можно поиграться с матрицами перед тем как делать что то.
```bash
DISPLAY=:0 xinput set-prop "wch.cn USB2IIC_CTP_CONTROL" 'Coordinate Transformation Matrix' 1 0 0 0 1 0 0 0 1
```
если после этого начало работать
правим: `sudo nano /etc/X11/xorg.conf.d/51-touch.conf` и вписываем правильную матрицу тача.

```bash
Section "InputClass"
        Identifier "ADS7846 Touchscreen"
        MatchIsTouchscreen "on"
        MatchDevicePath "/dev/input/event*"
        Driver "libinput"
        Option "TransformationMatrix" "1 0 0 0 1 0 0 0 1"
        Option  "SwapXY"        "1"
        Option  "InvertX"       "1"
        Option  "InvertY"       "1"
EndSection
```
перегружаемся.. испытываем счастье.

**Камера а клипперскрине**

Если у вас становлена вебкамера иногда надо подкрутить фокус, направить более правильно саму камеру на стол удобно использовать клипперскрин для отображения стола

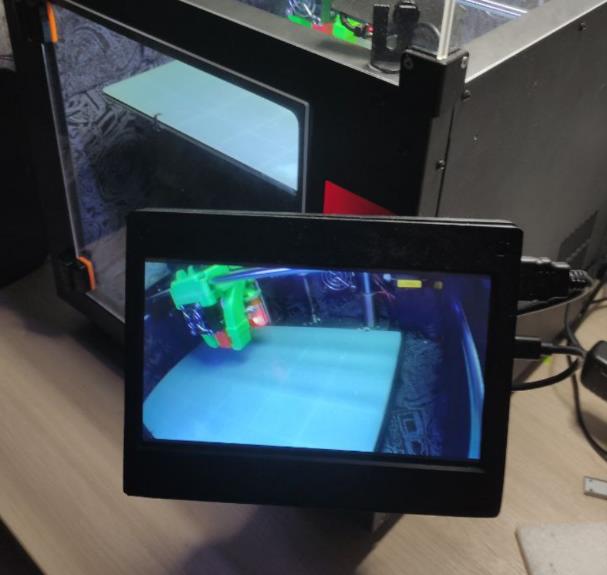
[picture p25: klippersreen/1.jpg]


Для этого в самое начало `klipperscreen.conf`  добавляем такую строчку:

```
[printer FlyingBear Ghost 6]
# Camera configuration
camera_url: http://127.0.0.1/webcam/?action=stream
```
после перезагрузки можем увидеть такую картинку:

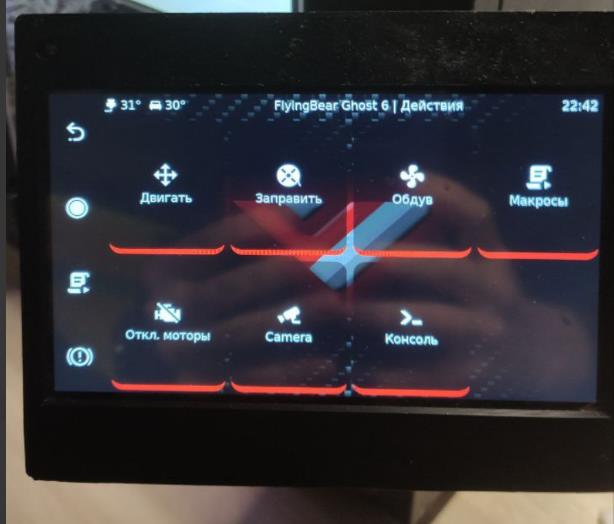
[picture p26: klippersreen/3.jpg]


но при нажатии вероятнее всего увидите вот это:

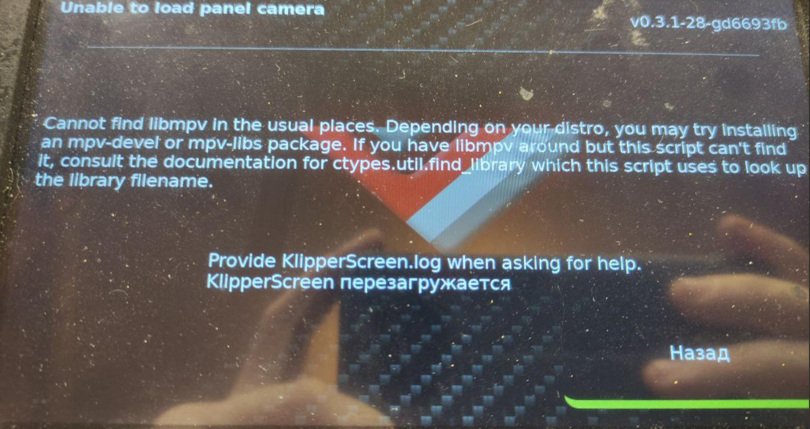
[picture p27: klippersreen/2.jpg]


для того чтобы исправить необходимо в консоли пишки(не клиппера) установить необходимый пакет:

```bash
sudo apt install libmpv-dev -y
```

после перезагрузки радуемся новому интерфейсу.

**если на клипперскрине неправильная ориентация камеры:**

к сожалению через клипперскрин конфиг поменять не получится, но есть выход отредактировать  файл webcam.txt что будет во всех смыслах более правильным решением

итак ищем строчку где наша камера например

```camera_usb_options="-r 1280x720 -f 20"```

и вписываем наш вариант поворота...  вот опции:
```
-rot: задать градус поворота (0-359, сработает коректно только 0, 90, 180  270)
-hf: горизонтальное отражение
-vf: вертикальное отражение
```
например для вертикального отражения наша строчка примет следующий вид:

```camera_usb_options="-r 1280x720 -f 20 -vf"```

P.S. у вас в опциях камеры могут свои настройки. данная строка просто пример!

не забудьте перезапустить сервис klipperscreen  для применения настроек.

**Выключаем пишку с клипперскрина**

В `klippersreen.conf`в самое начало файла добавляем:

```
[menu __main SHUTDOWN]
name: {{ gettext('Shutdown') }}
icon: complete
method: printer.gcode.script
params: {"script":"shutdown_machine"}
```
после перезагрузки в меню появится пункт "выключить" учтите, переспрашивать он не будет. так что нужно оно вам или нет думайте сами.

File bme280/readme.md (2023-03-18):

<h2>Подключение датчика температуры BME280</h2>

*update* [второй способ подключения](../i2c_mcu/readme.md)

При одинаковом названии есть два вида датчика, на 3.3 вольта и на 5 вольт. 
3.3 имеет 6 контактов и подключается как по i2c так и по spi, а вот версия на 5 вольт только по i2c.

картинка

в принтере есть датчик огня которые обычно не подключают и на его место bme280 прекрасно подойдет если хост расположен внутри корпуса как у меня.

картинка

необходимо протянуть дополнительный провод от хоста до датчика. 

1-VCC — питание модуля 5 В;

2-GND —  Земля (Ground);

3-SCL — линия тактирования (Serial CLock);

4-SDA — линия данных (Serial Data).

на orange pi 3lts подключим их в 4 6 5 3 разъем соответсвенно

картинка
 это было самое легкое. 

<h3>Настройка шины I2c</h3>
Запустим утилиту конфигурирования платы:  <b>armbian-config</b>. Перейдем по меню: System > Hardware, и включим <b>I2C0</b> после сохраняем, перегружаемся

скриншот

проверяем что работает

```bash
sudo i2cdetect -y 0
```
Шина I2C работает и датчик BME280 по адресу 0x76 найден 
картинка

Добавим пользователю возможность чтения шины i2c

```bash
 sudo usermod -aG i2c Имя_пользователя_поставь_свое
 ```
 Проверяем:

```bash
 id
 ```
 Должно быть что то похожее на это - ```uid=1000(klipper) gid=1000(klipper) группы=1000(klipper),5(tty),20(dialout),27(sudo),44(video),115(i2c)```

 <h3>Настройка Host</h3>
 Для использования orange pi как MCU с целью получения доступа к его шинам SPI, i2c и просто к GPIO, необходимо установить и запустить исполняемый модуль Klipper и на нем.

Для этого необходимо чтобы исполняемая часть MCU на orange pi запускалась раньше, чем загрузится Klipper, для этого выполняем следующие действия:

```bash
cd ~/klipper/
sudo cp ./scripts/klipper-mcu.service /etc/systemd/system/
sudo systemctl enable klipper-mcu.service
```

Действиями выше, был создан новый элемент автозапуска, и добавлен в скрипты загрузки.

Далее необходимо создать прошивку для Orange PI контроллера, для этого выполняем:

```bash
cd ~/klipper/
make menuconfig
```

В меню конфигурации, следует выбрать архитектуру процессора как Linux process, нажимаем Q и сохраняем изменения.
Теперь установим исполняемую часть на Orange PI:
```bash
make
sudo service klipper stop
make flash
sudo service klipper start
```

Теперь необходимо внести изменения в printer.cfg, чтобы Klipper смог получить доступ к MCU Orange PI
```cfg
[mcu host]
serial: /tmp/klipper_host_mcu
```
После выполнения этих действий и перезагрузки Orange PI вы получите доступ к шинам и GPIO вашего одноплатного компьютера.

чтобы датчик отображался добавим его в конфиг и добавим маленький макрос на будущее.
```cfg
[temperature_sensor Камера_принтера]
sensor_type: BME280
i2c_address: 118
i2c_mcu: host
i2c_bus: i2c.0

[gcode_macro QUERY_BME280]
gcode:
    {% set sensor = printer["bme280 Камера_принтера"] %}
    {action_respond_info(
        "Температура: %.2f C\n"
        "Давление: %.2f Миллибар\n"
        "Влажность: %.2f%%" % (
            sensor.temperature,
            sensor.pressure,
            sensor.humidity))}```
```
картинка

настройка i2c основана на этом мануале https://devdotnet.org/post/rabota-s-gpio-v-linux-na-primere-banana-pi-bpi-m64-chast-5-device-tree-overlays-shina-i2c-podkyuchenie-datchikov-bosh-bmx/
покупал датчик [тут] (http://alii.pub/6hx44l)

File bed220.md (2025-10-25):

### Перевод стола на 220V

Что нам для этого нужно?

Чтобы ваш Медведь мог очень быстро греть стол.

1. Грелка 200х200мм 220В. Я [поставил на 500W.](https://ali.click/z9j0n5)
   · Примечание: У нее есть небольшой нюанс — она с небольшим натягом влезает между винтами. В целом, с этим проблем нет, главное, чтобы грелка была размером 200х200мм.
2. [Твердотельное реле (SSR)](https://ali.click/agj0nm) (Это рандомное, которое я нашел. Насколько знаю, лучше всего брать оригинал FOTEK).
3. Шпатель из комплекта Медведя.
4. Изопропиловый спирт или что-то другое для очистки клея.

---

#### Установка

1. Снимаем стол с Медведя, откручивая барашки снизу.
2. Аккуратно отдираем весь утеплитель.
3. Берем шпатель и изопропиловый спирт и отдираем весь старый клей (процесс долгий, но спокойный).
4. Отрезаем старые провода ТОЛЬКО от грелки, на всякий случай оставляя небольшой запас.
5. Клеим новую грелку (распишу подробнее):
   · Откручиваем гайки.
   · Хорошенько приклеиваем новую грелку.
   · Закручиваем гайки обратно.
6. Убираем из кабельного канала («змеи») провода старого нагревателя.
7. Прокладываем туда же провода от нового нагревателя и его термистора.
   · ВАЖНО! Провода штатного термистора стола мы оставляем в «змее» и не трогаем.

---

#### Подключение

1. Достаем твердотельное реле (SSR).
2. Ищем на реле клеммы с маркировкой ~ 24-380VAC ~.
3. В один из этих разъемов подключаем один провод от новой грелки (не от термистора!).
4. Во второй разъем подключаем один провод от старой грелки (который мы отрезали ранее). Возможно, его нужно будет обрезать , чтобы он достал до блока питания с не слишком большим запасом(БП).

##### Далее работаем с блоком питания:

1. Находим на БП клеммы N и L (они подписаны).
2. На одну из этих клемм (например, L) подключаем провод от твердотельного реле (именно тот, который шел от старой грелки).
3. На вторую клемму (соответственно, N) подключаем второй провод, идущий напрямую от новой грелки.

Поздравляю, самое сложное позади!

Теперь нам остается только подключить плату управления к твердотельному реле и настроить все программно.

1. Ищем на плате управляющие пины для нагрева стола (те, к которым был подключен старый нагреватель).
2. Находим, где на этих контактах + и -.
3. От контакта + на плате ведем провод к клемме + на твердотельном реле.
4. От контакта - на плате ведем провод к оставшейся клемме - на твердотельном реле.

Всё, подключение готово.

Теперь немного о термисторе. Я оставил старый термистор и ничего не переделывал. Но вы можете подключить термистор, который находится на новой грелке. Здесь все зависит от вас. Лично я не вижу смысла его менять, пока он не выйдет из строя.

---

#### Настройка в прошивке Klipper

ПОМЕТКА! Это мануал для прошивки KLIPPER. Как все реализовать в MARLIN'е, я не знаю и знать не хочу.

1. Заходим в файл printer.cfg.
2. Ищем секцию [heater_bed].
3. Удаляем весь старый конфиг в этом разделе (все от [heater_bed] и до [fan](если у вас конфиг с гита)).
4. Вставляем на его место следующий код:

```
[heater_bed]
heater_pin: PA0        
sensor_type: EPCOS 100K B57560G104F
sensor_pin: PC0       
control: watermark
min_temp: 0
max_temp: 130
```

Вот и все, ваш Медведь теперь может очень быстро греть стол!

По вопросам пишите мне в ТГ: @niknikdm. Чем смогу — помогу.

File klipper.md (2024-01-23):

# Настройка Klipper для 3D-принтера FlyingBear Ghost 6 с подключением по USB

* одноплатник - одноплатный компьютер типа Raspbery Pi или Orange Pi (рекомендуется Orange Pi 3 LTS)

Опустим установку Klipper на одноплатник, про это есть много гайдов (например [этот](https://klipper.wiki/home/initial/base)), она не зависит от подключаемого принтера.

Итак, исходное положение, вы установили Klipper на одноплатник и рядом у вас стоит Flying Bear Ghost 6.

1. Необходимо скомплировать прошивку под ваше подключение, если вы подключаетесь по UART, то вам [сюда](mcu_uart/readme.md).
Если вы подключаетесь по USB то процесс настройки конфига прошивки и ее сборка следующие:

* в шелле пишем команду:

```
cd ~/klipper
make clean
make menuconfig
```

запустится псевдографический менюшный интерфейс для настройки конфигурации, выглядит так:

klipper menuconfig

Плата (модель процессора/Processor model) должна быть указана __407__

Bootloader (загрузчик) - __48Kb__

Интерфейс соединения - __USB__

Выбрав вышеуказанные настройки, выходим из конфигуратора, сохранившись

* далее нам надо собрать прошивку. Для этого последовательно запускаем две команды и ждем их выполнения

```make clean```

```make```

* Переходим в каталог, в который скомпилировалась прошивка ```cd ~/klipper/out``` и смотрим там листинг файлов ```ls -la```. Там должен быть файл с именем ```klipper.bin```.
Скачиваем его к себе (по scp или sftp - как это сделать, оставим вне этой инструкции) и переименовываем в ```Robin_nano_4.bin```.

Должно получиться что-то вроде этого:

![firmware_thumbnail](firmware_thumbnail.png)[скачать](Robin_nano_4.zip) распакуйте архив!

В имени файла не надо проявлять никакой самодеятельности, указанное имя должно работать. Однако, бывали случаи, когда получалось с ```firmware.bin```. Также, в принципе, можно взять чужой файл прошивки, но необходимо быть точно уверенным, что он сделан для того же принтера, а также типа и операционной системы одноплатника. Прошивка собирается на том железе, на котором будет работать. Поэтому способ 'взять у друга' нежелательный и извинит вас только то, что у вас лапки. :o)

2. Итак, загружаем получившийся файл на флешку, выключаем принтер, вставляем в него флешку, включаем... ждем пару минут для уверенности, выключаем принтер и вынимаем (!) флешку. 

Profit! Поздравляю, у вас ~~три~~клиппер! 

Теперь осталось несколько штрихов, чтобы начать свою первую печать.

3. Настраиваем конфигурационный файл

Практически готовый конфиг можно скачать здесь -> [printer.cfg](klipper_config/printer.cfg)

Но этого мало, для того, чтобы все заработало, надо правильно указать интерфейс соединения.

* Находим файл устройства (для этого принтер уже должен быть подключен шнурком по USB и включен). 

На одноплатнике выполняем:

```ls /dev/serial/by-path/*``` (также можно использовать ```/dev/serial/by-id/```)

должны увидеть что-то типа такого:

``` /dev/serial/by-path/platform-5101400.usb-usb-0:1:1.0```

* Ищем в printer.cfg строчку [mcu]

и записываем (через веб-интерфейс клиппера, который уже должен работать или открыв файл своим любимым unix-редактором vi.. ну или nano на худой конец.. а, да, можно скачать конфиг к себе на компьютер, отредактировать и закачать обратно, но в этом случае вы рискуете его запороть виндовыми редакторами :) ) туда то, что мы увидели на предыдущем шаге:

```serial: /dev/serial/by-path/platform-5101400.usb-usb-0:1:1.0```

Сохраняемся и мы готовы. Теперь надо все перезапустить для уверенности.

Когда все загрузится, мы можем уже зайти в веб-интерфейс Klipper на нашем одноплатнике.

Если вы все сделали правильно, то внутренний объём принтера осветится неземным светом стоковой светодиодной ленты, поздравьте себя чаем с плюшкой. Но перед этим найдите раздел макросы и тыкните на PID_B, подождите около 5 минут, и потом PID_E (и тоже подождите 5 минут) для регулировки термисторов у стола и экструдера. 

Вот теперь вы справились, добро пожаловать в мир  в котором нет пределов совершенству, теперь вы не сможете остановиться в улучшении своего принтера. 

Основано на конфиге и изысканиях от [Юрия Алексеева](https://t.me/Jura_Alekseev), проверка на практике, дополнения в конфиг и авторство текста принадлежит [Tom_Tomich](https://t.me/Tom_Tomich), редактировал и верстал [Korxif](https://t.me/Korxif)

Исправления, уточнения и улучшения, а также и вопросы с радостью принимаются на [нашем телеграм-канале](https://t.me/fbg5_waiters)

**P.S. выдержка из чата:**

*Небольшое наблюдение по вопросу необходимости обновления прошивки платы после обновления клиппера. 
Полезли у меня ошибки драйвера
TMC 'extruder' reports error: GSTAT:      00000001 reset=1(Reset)
Причём как-то странно, в одном-двух местах при начале печати, когда голова вниз идёт (в одном и том же месте) или когда линию просёра рисует. 
Ошибка была не всегда, если получалось начать печать без неё, то дальше печать шла нормально.
Почесал я репу, поменял драйверы. Не помогло. 
Пришло очередное обновление клиппера, обновил. Ошибки полезли и по другим драйверам и в других местах, но всегда в начале печати или при парковке. 
Ага, подумал я, я же клиппер несколько раз обновлял до этого, обновлю-ка я прошивку платы. 
Залил прошивку под текущую версию клиппера и ошибка пропала. 
Так что, не будьте, как я, не ленитесь обновлять плату после обновления клиппера.*

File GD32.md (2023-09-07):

Итак, коллеги, мы решили проблему с прошивкой новой ревизии принтеров. Огромное спасибо всем, кто принял участие, особенно @ub8cjz , который грамотно определил проблему, и @R_e_w_w_a_n который также консультировал по многим вопросам в данной проблеме. Для тех, кто еще не в курсе: в последней ревизии китайцы решили удешевить производство и вместо контроллера stm32, к которому по юсб подключались напрямую, поставили gd32 и использовали для подключения костыль в виде ch340. После прошивки на Марлин от Павла, или на сток с ЛА, а также сток в оф. сайта, вы больше не сможете получать команды с принтера по юсб и управлять им. Также на стоке с ЛА (на марлин не обратил внимания), принтер игнорировал команду из джикода на нагрев, в ручную работал(на новой прошивке еще не успел проверить). Данной прошивки пока нет нигде и выкладывается она впервые.

Почти наверняка пользователи перешитого марлина могут и не подозревать, что у них не STM32, а GD32, пока не попытаются подключиться по USB

[Марлин под Nano4 v3.2 - GD32+CH340, "красная плата"](/Ghost6-GD.zip)

На GD32 платы появились относительно недавно, в чате они не на слуху.

Первое значимое появление - проблема с клиппером, потребовалось указать, что соединение идёт через внешний USB-UART чип.
В тот же раз выяснилось, что клиппер не умеет на GD32 измерять собственную температуру кристалла, т.к. в чипе в OTP нет таблицы калибровки датчика температуры, в результате клиппер падал с делением на 0

В этом франкенштейне стоит чип GD32F407, связанный с миром по USB CH340.

При настройке клиппера для работы с USB нужно:
процессор STM32F407
бутлоадер 48К
тактовая частота 8МГц
Интерфейс связи USART3 (PB11/PB10)

НЕ РАБОТАЕТ термодатчик в MCU, ошибка "float divizion by zero" - закомментировать ВСЮ секцию [temperature_sensor mcu_temp]

При подключении платы к одноплатнику по UART доступен ТОЛЬКО порт USART1 на сокете WiFi. USART3 на четырёхконтактной гребёнке занят CH340



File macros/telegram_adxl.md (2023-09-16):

<h3 align="right"><a href="https://pay.cloudtips.ru/p/f84bf0b2" target="_blank">ваше "спасибо" автору</a></h3>

**Автоматизация теста резонансов для телеграм бота**

Если вы используете клиппер со встроенным акселерометром и когда-либо применяли тесты резонанса, вы, вероятно, хотели иметь возможность получать результаты прямо на выбранное вами устройство, а не загружать их вручную с принтера.

Благодаря возможности отправки изображений это стало реальностью, а не мечтой. Помимо клиппера и бота вам понадобится G-Code Shell Command Extension. Это позволяет выполнять команды оболочки, необходимые для выполнения соответствующего скрипта klipper python для обработки данных. 

1. Для этого необходимо запустить в консоли:

```
~/kiauh/kiauh.sh
```
выбираем 4 пункт "advanced" и там ищем "[G-Code Shell Command]" устанавливаем соглашаясь на всё) пишем "Y", выходим.



Иногда бывает проблема при копировании в windows и скрипт будет давать ошибки при попытке исполнения. 

2. тогда можно скачать его напрямую с гита к себе с помощью команды из консоли:

```
wget -P ~/printer_data/config/ https://raw.githubusercontent.com/Tombraider2006/klipperFB6/main/macros/shaper_calibrate.sh
```
Потом все равно не забудьте посмотреть и подправить путь до папки если пользователь не `pi`

**внимание! следующий текст это Второй вариант он для ознакомления и не рекомендуется!** 

2.1 *В папке с конфигами создаем файл `shaper_calibrate.sh` удобнее создать через Fluidd но это уж кому как). в него копируем следующий код:*

```
#! /bin/bash
OUTPUT_FOLDER=config/adxl_results/inputshaper
PRINTER_DATA=home/pi/printer_data
KLIPPER_SCRIPTS_LOCATION=~/klipper/scripts
RESONANCE_CSV_LOCATION=tmp
if [ ! -d  /$PRINTER_DATA/$OUTPUT_FOLDER/ ] #Check if we have an output folder
then
    mkdir /$PRINTER_DATA/$OUTPUT_FOLDER/
fi

cd /$RESONANCE_CSV_LOCATION/

shopt -s nullglob
set -- resonances*.csv

if [ "$#" -gt 0 ]
then
    for each_file in resonances*.csv
    do
        $KLIPPER_SCRIPTS_LOCATION/calibrate_shaper.py $each_file -o /$PRINTER_DATA/$OUTPUT_FOLDER/${each_file:0:12}.png # check
        rm /$RESONANCE_CSV_LOCATION/$each_file
    done
else
    echo "Something went wrong, no csv found to process"
fi
```
Не забываем исправить пользователя в строчке `PRINTER_DATA=home/pi/printer_data` если вас другое имя пользователя. 

3. через консоль сделаем файл исполняемым:

```
cd ~/printer_data/config/
chmod +x ./shaper_calibrate.sh
```

4. В `printer.cfg` добавим следущий блок:

```
[respond]

[gcode_macro telegram_shaper]
description: график шейперов в телеграм
gcode:
	{% set HZ_PER_SEC = params.HZ_PER_SEC|default(1)|float %} #Parse parameters
	{% set POSITION_X = params.POSITION_X|default(125)|int %}
	{% set POSITION_Y = params.POSITION_Y|default(125)|int %}
	{% set POSITION_Z = params.POSITION_Z|default(30)|int %}

	{% if printer.toolhead.homed_axes != 'xyz' %} #home if not homed
		G28
	{% endif %}
	TEST_RESONANCES AXIS=X HZ_PER_SEC={ HZ_PER_SEC } POINT={ POSITION_X },{ POSITION_Y },{POSITION_Z}
	TEST_RESONANCES AXIS=Y HZ_PER_SEC={ HZ_PER_SEC } POINT={ POSITION_X },{ POSITION_Y },{POSITION_Z}
	RUN_SHELL_COMMAND CMD=shaper_calibrate
	RESPOND PREFIX=tg_send_image MSG="path=['/home/pi/printer_data/config/adxl_results/inputshaper/resonances_x.png', '/home/pi/printer_data/config/adxl_results/inputshaper/resonances_y.png'], message='Результат проверки шейперов' "

[gcode_shell_command shaper_calibrate]
command: bash /home/pi/printer_data/config/shaper_calibrate.sh
timeout: 600.
verbose: True
```
Обратите внимание на строчки: 

1. `RESPOND PREFIX=tg_send_image MSG="path=['/home/pi/printer_data/config/adxl_results/inputshaper/resonances_x.png', '/home/pi/printer_data/config/adxl_results/inputshaper/resonances_y.png'], message='Shaper results' "`

 и 

2. `command: bash /home/pi/printer_data/config/shaper_calibrate.sh`  
 
 если имя пользователя не `pi` меняем на своё.

Работает это следующим образом:

1. Макрос вызывается с нужными параметрами, при необходимости возвращает оси в исходное положение и приступает к стандартному тестированию шейперов по обеим осям.
   
2. Макрос вызывает выполнение сценария, который запускает программу klipper python для каждого сгенерированного файла csv. Впоследствии он удаляет файлы csv, чтобы избежать путаницы при запуске нескольких тестов один за другим. Выходные изображения помещаются в подпапку в папке журналов, чтобы вы могли легко получить к ним доступ через веб-интерфейс, если это необходимо.
   
3. Макрос завершается отправкой обоих файлов вашему телеграмм-боту. Помимо того, что бот легко доступен, теперь он может выступать в качестве вашего архива измерений.



<h2>Добавим аналитики с помощью акселерометра.</h2>

Зачем устанавливают акселерометр на 3д принтер? изначально для измерения вибраций  более точного и простого способа для определения значений инпут шейпинга. в данном макросе собраны самые полезные тесты какие можно сделать с помощью установленного акселерометра.

**telegram_BELTS_SHAPER_CALIBRATION**



В данном графике с помощью акселерометра тестируются ремни моторов А(X) и В(Y) цель полчуть максимально совпадающие линии ремней- это сначит ремни натянуты одинаково, и привести к максимально похожему на один пик - минимальные вибрации 

**telegram_VIBRATIONS_CALIBRATION**

Данный макрос может формировать графики шейперов, анализ равномерности натяжения ремней, а также анализ зависимости вибраций принтера от скорости передвижения, что позволяет выбрать скорости с минимальными искажениями при печати и менее шумно.

Это полностью автоматизированный рабочий процесс, который работает путем перемещения головки инструмента при использовании акселерометра:

Он выполняет последовательность движений по оси, которую вы хотите измерить, с различными настройками скорости, при этом регистрируя глобальные вибрации машины с помощью акселерометра.

Затем он вызывает автоматический скрипт, который автоматизирует несколько вещей:
он генерирует график вибраций для указанной оси с помощью пользовательского скрипта Python.
Затем он переместит график в папку результатов ADXL.



На примере этого графика мы видим что основной пик вибраций приходится на скорость около 97 мм\сек если избежать этих соростей наш принтер будет менее шумным и печать более качественная. (у вас могут быть другие значения) 

**Внимание! коректные значения этого скрипта будут только после правильной настройки шейперов.**

| параметры | значение по умолчанию | описание |
|---:|---|---|
|SIZE|60|размер в миллиметрах области, на которой совершаются движения|
|DIRECTION|"XY"|вектор направления, в котором вы хотите выполнить измерения. Может быть установлен на «XY», «AB», «ABXY», «A», «B», «X», «Y», «Z» |
|Z_HEIGHT|20|z высота установки головки инструмента перед началом движений. Будьте осторожны, если ваш ADXL находится под соплом, увеличьте его, чтобы избежать столкновения ADXL с станиной машины |
|VERBOSE|1|Записывать текущую скорость в консоль|
|MIN_SPEED|20|минимальная скорость инструментальной головки в мм/с для перемещений|
|MAX_SPEED|200|максимальная скорость инструментальной головки в мм/с для перемещений|
|SPEED_INCREMENT|2|приращение скорости инструментальной головки в мм/с между каждым движением|
|TRAVEL_SPEED|200|скорость в мм/с, используемая для всех перемещений|
|ACCEL_CHIP|"adxl345"|имя чипа акселерометра в конфиге|

<h2>Установка</h2>

 аналогична предыдущему макросу:

 копируем файл к себе в папку скриптов.

```
wget -P ~/printer_data/config/scripts/ https://raw.githubusercontent.com/Tombraider2006/klipperFB6/main/macros/plot_graphs.sh
wget -P ~/printer_data/config/ https://raw.githubusercontent.com/Tombraider2006/klipperFB6/main/macros/vibr_calibrate.cfg
wget -P ~/printer_data/config/scripts/ https://raw.githubusercontent.com/Tombraider2006/klipperFB6/main/macros/graph_vibrations.py
```

через консоль делаем исполняемым:

```
cd ~/printer_data/config/scripts/
chmod +x ./plot_graphs.sh
chmod +x ./graph_vibrations.py
```
в `printer.cfg` добавим блок:

```
[include vibr_calibrate.cfg]

[gcode_shell_command plot_graph]
command: bash /home/pi/printer_data/config/scripts/plot_graphs.sh
timeout: 500.0
verbose: True
```

Не забываем исправить пользователя в строчке `PRINTER_DATA=home/pi/printer_data` если вас другое имя пользователя.

Обратите внимание на строчки: 

1. `RESPOND PREFIX=tg_send_image MSG="path=['/home/pi/printer_data/config/adxl_results/belts/`
2. `RESPOND PREFIX=tg_send_image MSG="path=['/home/pi/printer_data/config/adxl_results/vibrations`  

в файле **vibr_calibrate.cfg** который находится в основной папке. 

<h3 align="right"><a href="https://pay.cloudtips.ru/p/f84bf0b2" target="_blank">ваше "спасибо" автору</a></h3>

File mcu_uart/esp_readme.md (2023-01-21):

**Conexión de una impresora a través de UART**

La confucion principal se genera en los usuarios con la asiganacion del numero UART, memoricemos una regla comun: en printer.cfg anotamos el numero UART en single board,al compilar el firmware en el menu config escribimos el numero UART de la plaqueta de la impresora.
Conectamos como esta señalado en la foto.

```bash
sudo armbian-config
```
Sector system subsector hardware - activamos UART3



Modificamos el firmware para conectar UART

```bash
cd ~/klipper
make clean
make menuconfig
```
Micro-Controller architecture -  STM32

Processor model - STM32F407

Bootloader offset - 48KiB bootloader

Comunication Interface - Serial (on USART1 PA10/PA9)



Presionamos Q guardando los cambios y compilamos el firmware.

```
make
```
El firmware esta compilado y se encuentra en la carpeta
 ~/klipper/out/klipper.bin lo retiramos y lo renombramos Robin_nano_4.bin, lo copiamos 
a la tarjeta de memoria y prendemos la imresora.La instalacion del firmware ocupa algo
de un minuto.Si el firmware se instalo correctamente en sutarjeta de memoria aparecera
 el arcivo Robin_nano_4.cur OrangePi 3 LTS para la coneccion UART utilice overlay UART3 y /dev/ttyS3.

En printer.cfg buscamos mcu y cambiamos por
```
[mcu]
serial: /dev/ttyS3
restart_method: command
```
abajo se muestran las fotos donde se colocan los cables.




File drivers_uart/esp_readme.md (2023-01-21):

Coneccion de los drivers UART

Los drivers por defecto en modo silencioso.Todo lindo,solo que a las velocidades por arriba de 100 empiezan a hacer ruido y gritar como locos.Claro que se puede imprimir a la velocidad de 300 y no prestar atencion,pero se puede hacer soldaduras por UART y desactivar este modo. Aca esta el ejemplo antes y despues... -mirar con sonido.

https://user-images.githubusercontent.com/59514540/202737043-5a83339d-8136-49bd-a743-e7dec3daad25.mp4

https://user-images.githubusercontent.com/59514540/202737096-bd7b8f84-f78c-458d-82d0-08003b43714e.mp4

mejor consulte al profecional! (se lo adverti)
Desoldar las resistencias (metodo viejo,se puede no desoldar nada) y soldar los cables como se indica en la foto

ATENCION! despues de soldar cubra el lugar de la soldadura con termopegamento,ya que por la vibracion los cables pueden despegar las pistas.

En `printer.cfg` agregamos `[include tmc.cfg]` ¨copiamos el archivo [tmc.cfg](tmc.cfg) a la carpeta te 
clipper al lado del archivo `printer.cfg`
Es necesario corregir microstep en las configuraciones de la imresora y configurar los pasos del extructor,en este momento una parte de mi printer.cfg se ve asi:

```cfg
[stepper_x]
step_pin: PE3
dir_pin: !PE2
enable_pin: !PE4
microsteps: 16
rotation_distance: 40
endstop_pin: !PA15
position_endstop: 1
position_max: 255
homing_speed: 40

[stepper_y]
step_pin: PE0
dir_pin: !PB9
enable_pin: !PE1
microsteps: 16
rotation_distance: 40
endstop_pin: !PD2
position_endstop: 1
position_max: 220
homing_speed: 40

[extruder]
step_pin: PD6
dir_pin: PD3
enable_pin: !PB3
microsteps: 16
rotation_distance: 7.839
max_extrude_only_distance: 1400.0
nozzle_diameter: 0.400
filament_diameter: 1.750
heater_pin: PE5
sensor_type: Generic 3950
sensor_pin: PC1
#control: pid
#pid_Kp: 14.669
#pid_Ki: 0.572
#pid_Kd: 94.068
min_temp: 0
max_temp: 320
pressure_advance = 0.022
```
Como por ahora no tengo conectado el eje Z por UART (esto no hace falta en 99.9% de los casos).Su configuracion no esta descripta aca para no confundirlos.Su propia configuaracion del eje Z la dejamos por defecto.Presten atencion que los numeros en sus impresoras pueden ser diferentes.El coeficiente pressure_advance es una configuracion aproximada que para ustedes no significa nada,configurenla ustedes mismos.






Si hacen todo de forma correcta tiene que salir asi:



P.S. DEspues de que ustedes hicieron todas estas operaciones y empezaron a imprimir van a escuchar ruidos extraños y fuertes al imprimir las primeras capas a baja velocidad. Ypor que esta pasando esto?

Por defecto los drivers estan conectados en "modo silencioso" llamado stealthChop justamente este "modo silencioso" producia el ruido a la velocidad elevada y despues de conectarse por la UART ustedes pasaron a modo spreadCycle, que es rapido y mas precizo que puede hacer ruido a las velocidades bajas. Hay configuracion para cada uno de los motores para activar el "modo silencioso"... Se podria activarlo,la documentacion describe que a las velocidades mas bajas que las establecidas estos modos se activan entre ellos... Pero.......

Voy a citar la pagina oficial de Clipper: "Siempre se recomienda utilizar el modo «spreadCycle» (sin declarar stealthchop_threshold) o utilizar siempre el modo «stealthChop» (configurando stealthchop_threshold al valor de 999999). Lamentablemente los drivers a menudo dan los resultados malos y confusos si el modo cambia cuando la velocidad del motor no es igual al 0".

Por eso en algun momento vamos a poner stealthchop_threshold: 120 y a la velocidad mas baja que 120mm/s el driver pasara al "modo silencioso", pero esto no va a pasar ni hoy ni en los proximos tiempos.

Que tenemos que hacer? Aprender aimprimir a las velocidades que no fueron impuestas por los "ancianos",sino utilizar los shapers para compensar las resonancias y Pressure advance.Y hasta el ruido este pequeño aparentemente se va a aparecer solamente en las capas primarias

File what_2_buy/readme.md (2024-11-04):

**Что купить.**

Перед каждым владельцем принтера встает вопрос что купить для исправления известных косяков китайского чуда техники, что нужно для лучшей печати и что необязательно. Универсального ответа не существует, так как финансовые возможности у всех разные и цели покупки тоже. Рассмотрим несколько вариантов для возможного апгрейда. Также я постараюсь пояснить что и для чего.

**Must have** *обязательный набор*

1. сопло и термобарьер - он же горло. В комплекте с принтером на данный момент поставляется довольно странный выбор, в стандартный блок V6 воткнули сопло MK8 сквозной стальной термобарьер. Чем плохо это решение? Тем что на температурах более 250 трубка внутри достаточно быстро деградирует, а учитывая её качество и с гораздо меньшими температурами. Толстое горло слишком хорошо проводит тепло и шанс словить пробку даже на PLA достаточно высокий. Что делать? Заменить горло на биметаллическое или титановое, ~~но тут возникает диллема, радиатор тоже далек от стандарта и у нас возникает 2 выбора, купить высокое гладкое 17мм основание или короткое с основанием 13.5 мм, длинное придется подпиливать на 2 мм, а короткое высунуть на 2 мм, потому, что сопло нужно сменить на e3dv6 у которого более длинная резьба и оно идеально стыкуется с горлом внутри хотенда. Мой выбор короткое горло [тут](http://alii.pub/6i45v0) и сопло [тут](http://alii.pub/6i45y4)~~ 

  покупаем термобарьер [тут](https://rrf3dshop.ru/catalog/komplektuyushchie/termobarery/bimetallicheskiy-e3d-v6-termobarer-gladkiy-fbg/)  или [тут](https://aliexpress.ru/item/1005005363535464.html)

   сопла обычно надо 0.4 и для технички 0.6 выглядит горло так так

после установки будет выглядеть так 

так



подробная инструкция [тут](https://fb-waiters.bibirevo.net/hardware/fbg6/bimetall)

2. **Адгезив**. Конечно опытные 3д печатники прекрасно знают кучу рецептов и тут мои советы совершенно излишни, мне понравились адгезивы от https://fdmartel.ru Есть несколько температурных градаций, хорошие наборы. 

3.  **Термисторы, Нагреватели** Если вы опытный печатник, то вы тут вообще делаете? Листайте ниже, эти советы не вам.  Если неопытный, поверьте, термисторы и нагреватели это такой же расходник как и пластик и желательно иметь запас, в стоке стоят термисторы [ATC Semitec 104NT-4-R025H42G купить](https://www.ozon.ru/product/termistor-atc-semitec-104gt-2-v-gilze-ot-trianglelab-618437315/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) но я рекомендую простые 3950 например [тут](http://alii.pub/6i45pr) и нагреватели 40 -50 ватт например [тут](http://alii.pub/6i45p6)

4.  **Силиконовый носок** Как мы жили без них? Плохо жили, обмотки каптоновым скотчем.. Брр.. Сейчас проще - покупаем вид V6 PT100 -Blue [тут](http://alii.pub/6i4618) Сколько? Да сколько не жалко, запас карман не тянет, а стоят они недорого.

5. В стоке родная коса проводов от корпуса к фидеру идет в пластиковой гофре, она тяжелая, скрипучая и неудобная, меняем ее на [эту](http://alii.pub/6i479y) вид - 10мм

5. **Трубка PTFE** расходник. Если будете менять горло и чуть ошибетесь с подрезкой родной трубки тоже пригодится купить можно [тут](http://alii.pub/6i47x3)

6. В процессе использования принтера нам необходимо его обслуживать и откручивать закручивать множество винтиков. К сожалению многие из них сделаны из марки стали "пластилин М3" да и потеряться, закатиться такая мелочь ой как любит, рекомендую купить [такой](http://alii.pub/6i48k8) набор, чтобы компенсировать данное неудобство.

7. На современные ревизии вместо стекла ставят магнитную подложку и пеи пластины. качество их может вызывать вопросы. Наш земляк из челябинска производит альтернативое адгезивное покрытие на популярные модели принтеров по уникальной методе.  Это сендвич из 0.5мм пружинной стали и 0.5 FR4. Главная особенность fr4 - можно печатать таким отличным инженерным пластиком как наполненный полипропилен БЕЗ клея. Для остальных пластиков советую использовать адгезив. + возможно печатать как на стороне с текстолитом, так и на металле. при стоимости +- как поделие китайцев вы получаете очень долговременное прочное качественное покрытие для вашего стола. [**купить можно тут**](https://www.avito.ru/chelyabinsk/orgtehnika_i_rashodniki/pokrytiya_dlya_3d_printerov_fr4_na_stalnoy_podlozhke_4084946323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) (за рекламу денег не просил и не давали. классная штука реально)

8.  А в общем то и всё. Можете мне написать, что я забыл, но для старта печати вам в общем-то ничего больше и не надо. Кроме пластика конечно. Но вы же только положили в корзинку и увидели что траты совсем небольшие и готовы продолжать? Тогда переходим в раздел:

**Аdvanced** *продвинутый от начального*

 В этом разделе будут товары которые необязательно покупать, но которые существенно или не очень улучшают принтер вне зависимости от прошивки. Например:

   1. **кулера обдува модели** [4010 от gdstime](http://alii.pub/6i49f5) нам нужны dualball на 24 вольта существенно тише штатных и за счет увеличенного количества оборотов в минуту более производительные.

   2. **heatblock V6** не штатный порошковый, а нормальный фрезерованный алюминий [купить тут](http://alii.pub/6i49pu)

   3. **Сушилка для пластика** Тот же PetG может сильно набирать влагу и после этого нормально печатать им просто не получится, как бы вы не играли с настройками. [купить можно тут](https://alii.pub/6jxzzk)

   4. **Дихлорметан** достаточно ядовитый растворитель, но незаменим для обработки PLA и PetG пластиков [купить можно тут](https://market.yandex.ru/offer/adM95eCRRXghq39tuy6s3Q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)

   5. **Основание Fr4** на замену ультрабазе и для печати пластиками типа нейлона, но также подходящее и для остальных можно купить [такой текстолит](http://alii.pub/6i4ayk). Нарезан уже в размер мишкиного стола. брать 2 мм толщину оптимально по цена\качество.

   6. **Щетки очистки сопла** можно использовать как напрямую, так и сделать автоматическую чистку из моего [мануала тут](../clean_nozle/readme.md) купить [тут](http://alii.pub/6hz9dc)

   7. **подшипники оси Z LMK12LUU** пока статистики недостаточно. (скорее необязательный пункт) [купить тут](http://alii.pub/6i4w92) родные подшипники внутри сухие! рекомендую как минимум смазать.

   8. **Линейные подшипники LM8LUU, 8 мм, 8 на 15 на 45 мм 4шт** по сообщениям сообщества есть случаи больших зазоров в линейных подшипниках на осях. [купить тут](https://alii.pub/6m01fk)
      8.1 Рекомендую все же рассмотреть к замене подшипники или, как минимум, разобрать и набить смазкой.

   9.  **Смазка для линейных подшипников** ох и спорный пункт, не в том, нужна ли смазка или нет, но сколько же копий ломается в чатах о том, какая именно она должна быть. Решил дать ссылку от производителя принтеров, какую уж покупать решите сами. [вот ссылка](https://aliexpress.ru/item/1005003723700768.html)
  1.  **Провода AWG24** Я лично уже заменил из-за своей криворукости, но мне писали что есть проблемы не только у меня. Для замены проводов мне понадобилось около 8 метров чтобы заменить 6 проводов которые идут к плате на фидере. еще 4 провода идут к мотору. итого я рекомендую купить 4 раза по 5 метров по [этой ссылке.](https://alii.pub/6j28ox) Рекомендую 1 красный 1 синий и 2 черных. по 5 метров каждый. **или** по [этой ссылке силиконовые провода](https://alii.pub/6jprii) 
  2.  **Разъем PHB 2.0** чтобы скомутировать ваши новые провода вам понадобиться [разъем и концы под обжим](https://alii.pub/6j28vc) 
  такие 

**Klipper begginer**

  Для современной печати первое что нужно понять что марлин был хорош, но он уже сдает свои позиции и вероятнее всего никогда уже не отыграет их назад, чтобы воспользоваться всеми достижениями прогресса необходима прошивка **klipper**. Апологетов этой прошивки сейчас на каждом канале и почти у любого ютубера есть видео о ее достоинствах и фишках. в данном мануале нам важно, что многие вещи возможны только на ней и многие вещи нам нужны будут только для этой прошивки, в первую очередь для различных подключений,  с учетом возможностей которые дает эта прошивка. 

   Как в сказке начинают от печки мы начнем с блока питания. 

   Рекомендую перейти в раздел [placement](../placement/readme.md) и посмотреть на вариант реализации размещения внутри принтера. не испугались и даже выписали ссылки? Ну и чудненько, читаем дальше. Из вариантов питания можно еще купить  [понижайку на 3 ампера с 24 до 5 вольт](http://alii.pub/6i4dya), но мой вам совет, купите нормальный блок питания для одноплатника.  

   Итак, нам потребуется:

   1. **одноплатный компьютер** он же апельсинка, малинка, пишка, хост, "он же Гога он же Гоша"(с) на данный момент малинка raspberry стоит неадекватно денег поэтому народный выбор это Orange pi 3 lts которая  спокойно держит необходимые требования, обладает кучей достоинств и практически не имеет недостатков учитывая ее цену. [купить тут](http://alii.pub/6i4egk)

   2. **радиаторы охлаждения** [купить тут](http://alii.pub/6i4ejh) Многие могут сказать что работает и так и можно поставить обдув рядом, но я вспомню фразу М. Ю. Жванецкого "врачи у нас лечат и так, но лучше заплатить"(с) 

   3. **набор проводов dupont** не надо в меня кидать сразу тапки, да это временное соединение и на постоянное его использовать советовать не буду, но многие используют и в качестве проверки работоспособности они незаменимы, ну а если добавить пару капель из термопистолета то и на постоянное сойдет. Купить хороший набор [можно тут](http://alii.pub/6i4fzs)

   4. **наборы разъемов** [XH2.54 набор ](http://alii.pub/6i4g7d),  и инструмент для [обжима](http://alii.pub/6i4ggb)

   5. **провода тонкие** я брал [тут](http://alii.pub/6i4goo) косу по 10 и три метра. Пригодились при подключении акселерометра. Почитать можно [тут](../adxl345_2_mcu/readme.md)

   6. **акселерометр ADXL345** [брал тут](http://alii.pub/6i4hje)

   7. **светодиодная лента** самый дешевый и эффективный вариант на данный момент это 144 диода на метр при питании от 5 вольт [купить тут](http://alii.pub/6i4gz6) почитать о подключении можно [тут](../led_rgb/readme.md)
   8. **UART-USB** Он копеечный, но может здорово выручить. Также удобен при начальной настройке - не надо монитор с клавиатурой, не надо ethernet, не надо править образ, задавая wifi ssid/пароль ДО первого старта. [CP2102](https://aliexpress.ru/item/32694152202.html) или [CH340](https://aliexpress.ru/item/32529737466.html)

   9. **Экран 7 дюймов** на замену. Я наверное один из первых кто запустил родной экран мишки как klipperscreen и могу с уверенностью вам сказать что оно того не стоит, трудность установки, танцы с бубном вокруг подключения и конфигурирования, не дадут вам удовлетворения из-за отвратительного качества резистивного экрана с плохим откликом и жуткими артефактами. Не мучайте дохлую лошадь - слезьте и купите хороший экран с быстрым и простым подключением легкой настройкой, а главное полноценным использованием для чего все это и затевалось. Поверьте тому человеку который прошел все стадии принятия от торга до гнева и депрессии) [купить дешево тут](http://alii.pub/6i4irx) и уж точно дешевле вашего потраченного времени и сил в битве со стоковым экраном. 

    

   модельку под    него можно скачать [тут](https://www.thingiverse.com/thing:5629418)

  9.  **акриловый колпак** Стало тише, что странно, ну и он точно лучше стокового недоразумения. Купить [тут](http://alii.pub/6i4m86)

   10.   **Веб камера** Это наверное один из самых сильных аргументов который подвиг меня на установку klipper. Возможность записывать таймлапсы, следить за печатью не подходя к принтеру. Основной параметр при покупке - `mjpeg-streamer`  это почти все камеры, дальше на вкус и кошелек, я взял logitech c270 сейчас их лучше искать на Авито или вообще подобрать вариант на али с модулями и распечатать на них корпус. Также важным качеством для камеры будет угол обзора, я вышел из положения докупив [линзы](http://alii.pub/6i4vxs), более правильным вариантом будет подбор модуля камеры уже сразу с широким углом, от 120 градусов.
  
  11.  [**Ремни GT2 6mm**](https://alii.pub/6khl1y) Справочный пункт. родные ремни хорошего качества и смысла менять их сразу нет. Однако если вам придет в голову это сделать длина ремня икс 143 см игрек 147 см. так что для покупки вам достаточно купить 3 метра а не 4 как многие советовали раньше. чтобы сменить ремни не мучаясь подсобными инструментами есть простой способ: капля супер клея на кончик ремня. сжать пасатижами и аккуратно тянете за противоположный конец. 
   

  **ULTIMATE** 

  Один из самых основных недостатков мишки 6 это огромные для директа ретракты. Люфт шестерни, неправильная геометрия задника фидера, неправильный модуль шестерен это все равно только половина проблемы, даже замена фидера все равно оставляет порядка 70-80мм от шестерен до кончика сопла. Если хочется печатать флексами то это будет боль и страдания с черепашьими скоростями поэтому как говорили индейцы: если лошадь сдохла - слезь. Можно загнать ладу семерку в автоцентр компании лотус, но после этого мы получим все равно ладу, аэродинамику и вес кирпича. так и здесь. переделывать фидер можно, менять моторы на более легкие.. но главный недостаток это не изменит.  На данный момент есть несколько решений и одно из них это 
    
  [**BIQU H2 v2**](https://alii.pub/6ib1vi)  *на данный момент продается только версия VS в которой изменения небольшие, подходит версия от misago*
    , хоть и не новое, но проверенное имеющее самые лестные отзывы от известных топовых блогеров. Малый вес, компактность и главное прекрасные характеристики при печати флексами, а значит и остальными пластиками выводят этот экструдер в неоспоримый топ. при покупке я основывался на обзорах [Дмитрия Соркина](https://www.youtube.com/c/SorkinDmitry) на  [этом](https://youtu.be/2bxKz0nOVpY) сравнении и [обзоре предыдущей версии](https://youtu.be/n_B7iGDqVm0) экструдера.

   Модель каретки  для печати можно [скачать по ссылке](../karas/readme.md)

   
   
   

**Интересное**
https://a.aliexpress.com/_Ex77ngD кому не лень, подпишитесь на магаз, это запчасти для принтеров с которыми нашли общий язык итальянцы, они делают на заказ для 5 и шестых мишек всякое разное, кстати интересные сопла у них есть и пеи на мишку с интересным рисунком. магазин реально интересный и ребята из итальянского чата пообещали если подписок на магаз будет много будут появлятся разные кастомные вещи под 5-и 6 мишку.

  [**Моторы на замену стоковых ХY**](https://www.duxe.ru/catalog/dvigateli_1/shagovye_dvigateli/shagovyy_dvigatel_42hs60_1504/) Шаговый двигатель 42HS60-1504 

  **отзывы:**
    
  "они в несколько раз тише. Мне так как никому другому это заметно. У меня в одной комнате 2 Реборна печатают с одними и такими моторами"

  "Ну первое что - нет вибраций, у меня на 150 ммс они были по раме от моторов, сейчас нет вообще"

  "Так же резонансное гудение процентов на 70 меньше стало. Оно теперь намного тише и намного реже"

  

  [**Виброизоляция**](https://www.ozon.ru/product/vibroizolyatsiya-dlya-plastika-dreamcar-vibrokorrektor-2mm-bolshoy-list-0-7h0-5m-4-276363499/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) 

   Нам нужны 2мм толщины, минимум 2 листа.  Вибрация согласно средствам инструментального контроля таким как акселерометр не уменшилась,  но шум принтера особенно на высоких частота глушит хорошо.  исключительно если вы фанат и вам хочется. 

  [**Платы на замену**]

  Как уже упоминали, на плате выгоре какой-то мосфет управления вентилятором, и втянул за собой микроконтроллер stm32f407vet6. В теории ремонтируется, но в РФ stm32 в розницу стоит примерно 2000р, что уже очень близко к новой плате целиком.

Варианты замены платы:

1. [Mks Robin Nano V3.1.](https://alii.pub/6l3av0) Механически встаёт на место родной, электрически совместима на 98% (нет управления родной светодиодной лентой, и надо 2 вентилятора в 1 разъем подцепить). В принципе, даже стоковая прошивка (и прошивка от Паши) заработает, если правильно настроить перемычками микрошаги и подобрать направление вращения моторов.
Цена около 3000р в комплекте с драйверами.

1. [Btt Skr Mini](https://alii.pub/6l3avz) - компактная плата с распаянными драйверами, около 2500р. Потребует творческого подхода в креплении, подключении и конфигурировании. Можно собрать Marlin, но потребуется и экран поменять. Более разумно использовать с клиппером.

2. [Btt Skr Pico](https://alii.pub/6l3axq) - самый бюджетный вариант для замены, около 2000р (но мосфет стола работает на пределе, рекомендуется дополнительный силовой ключ для управления столом)

На момент изучения эта плата работала исключительно с прошивкой клиппером, подключение дисплеев не предусмотрено.

4. Практически любая плата управления принтером, в зависимости от толщины кошелька и угла заточки рук

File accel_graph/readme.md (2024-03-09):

<h3 align="right"><a href="https://www.tinkoff.ru/rm/yakovleva.irina203/51ZSr71845" target="_blank">ваше "спасибо" автору</a></h3>

**Как перестать беспокоится и научится читать графики акселерометра**

Для начала чуть теории, чтобы при остановке движения не было остаточных качаний движение делится на несколько "пинков" и когда докатывается до конечной точки не остается сил на колебания. ZV - 1-2 пинка, MZV - 2-4 пинка и так далее..  чем больше пинков и тем меньше контроля между ними и более скругляется угол прохождения,  поэтому  если важна точность(сопряжение деталей, высокодетализированная художественная печать) рассматривать шейперы шире чем  MZV не стоит.  Важно понимать, что любой шейпер перекрывает не четко 1 частоту а некий диапазон, поэтому  десятые доли это скорее прикладывание подорожника к отсеченной ноге.(на графиках каждый из шейперов показан пунктирной линией своего цвета.что интересно, шейпер может гасить и вторичные колебания за счет своей синусоидальной структуры). если одна ось показывает прекрасные результаты, а вторая плохие то вы все равно инвалид и показывать олимпийские результаты бега не сможете. важно отрегулировать обе оси для хороших результатов и рассматривать их в совокупности. 

пример работы алгоритма (https://youtube.com/shorts/bzNB46Av740?feature=share)

*Сначала предлагаю посмотреть видео Дмитрия Соркина ["что не так с инпут шейпингом"](https://youtu.be/ZFPkfZEB-XU)*

после того как вы получили график теста по осям нужно понять есть ли у вас проблемы, какие они и можно применять шейперы которые вам порекомендовал автокалибровщик.



1. размерность. грубо говоря в какой степени количество ноликов в наших вершинках. тоесть если написано 1е3 это 1000 если 1е5 это 100000 
2. высота вершинок множим на размерность.. 
3. предлагаемые шейперы автокалибровщиком. имя шейпера, частота шейпера. процент остаточных вибраций после его применения.  Сглаживающее время. и ускорение. 
4. предлагаемый шейпер автокалибровщиком.
5. цветом обозначены графики по осям, отдельного внимания заслуживает голубая линия - предполагаемый график после применения рекомендуемого шейпера.
   
Теперь подробробнее по некоторым из пунктов.  

   1. Главная ошибка которую вы можете допустить это игнорировать размерность. график может выглядет красивым и близким к идеалу только потому что настолько огромен что остальные недостатки просто тонут в его высоте. и наоборот при размерностях 1е2-1е3 небольшие шероховатости могут выглядеть  огромными проблемами. 
   2. менее важный параметр но все равно 8 больше чем 1 и это надо учитывать в сравнении если вы делает несколько замеров после исправлений. 
   3. Выбор шейпера. первое на что я обращаю внимание это процент остаточных вибраций. он должен быть близким к нулю или быть равен нулю. второе это разрыв в ускорении первого шейпера и последующих.. например первый шейпер 27100 а второй 10300 это снижение в более чем два раза, значит что проблема есть, вне зависимости что нарисовано на графике, толку не будет. при шейпере скажем 12к и на ZV 9к на MZV это вполне допустимо.  если смотреть на график из первого примера даже несмотря на то, что мы видим достаточно малую размерность, мы понимаем что нормально данный принтер работать не будет и менять частоту шейперов это как переставлять кровати в борделе, менять надо не их, а работниц. в нашем случае разбираться с кинематикой. как с этим бороться мы рассмотрим далее.

Если все не так все так и плохо после первых данных рассмотрим сам график



В данном примере мы можем предположить на основании вышесказанного что все достаточно неплохо, и предложенный шейпер будет работать вполне неплохо. Но есть несколько проблем:
1. рваный спуск у основного пика. часто говорит о том что у вас есть незакрепленные элементы  кинематики, проверьте как закрплены моторы, затянуты ли винты на подшиниках осей.
2. дополнительный пик поймать гораздо тяжелее,  да он тоже рассказывает о некой проблеме, но это уже может быть плохо стянутый корпус, неустойчивое основание, разболтанные стойки вертикальные. высокая частота около 87 герц дополнительно указывает что дребезг искать придется долго и последовательно.  внимательный читатель заметит что колебания идут по оси зет, хотя меряли вроде игрек, это ошибка составления конфига, в нескольких местах мануала это еще будет встречаться. 

Следующий пример:



В данном случае мы видим размерность 1е4 что неплохо,  0.0% в остаточных вибрациях рекомендуемого шейпера. сам пик один, без дополнительных зубцов на подьеме и спуске.  есть небольшой дефект на самой вершинке, но в целом если вы получили такой график. можете расслабится и смело применять автокалибровку к вашему конфигу.  

  А теперь рассмотрим пример когда автоматическая калибровка будет нести открованную чушь. если посмотреть на предыдущий график, то голубая линия после применения шейпера это размерность нашего следующего графика.



Итак смотрим размерность 1е3 - очень хорошо, смотрим ускорение первого шейпера -2000? ЧТО??  уже интересно, смотрим частоту предлагаемого шейпера 46?  несмотря на то что основной пик на 75 герцах? ну ну..  

Итак что же случилось и почему так произошло? дело в том что алгоритм вычисления шейпера плевал с высокой колокольни на размерность, и пик в районе 20 герц который на графике 1е5 мы бы даже не заметили вырос близко к основному пику, алгоритм попытался заткнуть их обоих и переместил с 75 герц основного пика колебаний на 46.8 что то между .. "И нашим и вашим и еще мы пляшем..."  да еще и максимальные ускорения опустил ниже плинтуса..  что делать в этом случае? конечно сначала поискать что там у нас так ругается в районе 20 герц, учитывая размерность дергается несильно поэтому не факт, что поиски увенчаются успехом. второе это поставить шейпер вручную на основной пик и просто проигнорировать малый, решение было бы не лучшим если ваша размерность 1е4 или 1е5 но вполне допустимая если 1е2 или 1е3 в данном случае учитывая что сама высота пика 0.8. 

После того как разобрались с каждой осью отдельно стоит рассмотреть их вместе. 

Если на одной оси приходится выбирать шейпер, который ограничит ускорения цифрой N, то на второй оси имеет смысл поставить самый жесткий шейпер, который ограничит ускорения цифрой не меньше N. То есть, если на оси Y шейпер даёт ускорения до 10к, то не имеет смысл на Х пытаться поставить такой шейпер, который даст ограничение 20-30к ускорения. Лучше поставить шейпер, который даст 10-12к ускорения, но погасит больше вибраций. 



**Что делать с плохим графиком?**

Первое, сначала четко определится с картой осей. 

```axes_map: x,y,z```

Как расположить правильно? на акселерометре нанесена разметка

![](adxl.jpg)

 Оси должны быть расположены в сторону роста координат. в большинстве случаев это слева направо по икс и от себя по игрек,  если акселерометр установлен плоскостью платы вертикально распиновкой вверх то применяем следующий лайфхак:

```axes_map: -x,-z,-y``` 

возможно не с первого раза но вы сможете поймать оси правильно. 

По моему скромному мнение -+ не столь нужно и на качестве графика не сказывается. 

**Для чего важно делать правильную карту?** 

если вы будете делится вашими результатами в сообществах и чатах и спрашивать совета, нужно чтобы не было двоякого мнения какая ось за что отвечает.

**Каждая модель принтера имеет свои болячки**

Бесполезно бороться с некоторыми дефектами заложенными в конструкции, но есть наработанные сообществом нормы. для 6 медведя нормально иметь основной пик графика в районе 50-75 герц по  осям и ускорения на правильно настроенном принтере 8000-12000.  Это не догма, если вы смогли добиться 16 тысяч это прекрасно, но если у вас максимум 5000 это повод задуматься о том чтобы перебрать кинематику. 

Есть один нюанс у мишки 6  - это его консольный стол. при высоких скоростях сопло при переходе может вызывать вибрацию стола.  колебания стола могут не успеть успокоится когда сопло начинает печать в новом месте. я выхожу из положения настройкой подьема головы в CURA,  причем как при переходе на новый слой так и при откате и при перемещениях над напечатанной деталью. 

**Самое главное**
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

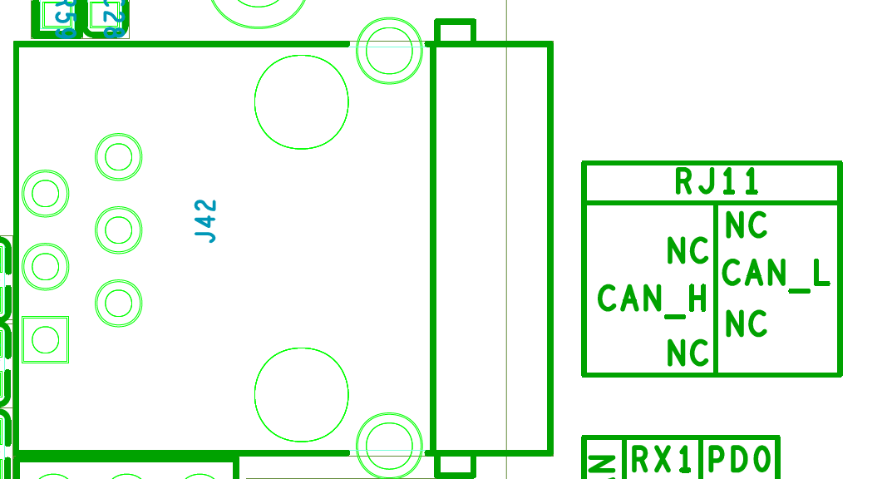
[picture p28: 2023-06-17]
tune-up/ebb_can/pinout.png

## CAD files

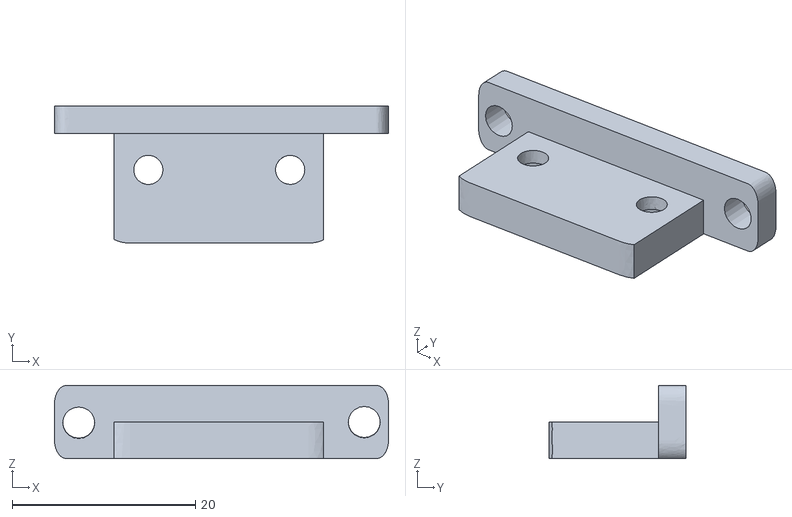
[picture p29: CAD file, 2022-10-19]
adxl345_2_mcu/adxl2.stl
36.5 x 15.0 x 8.00

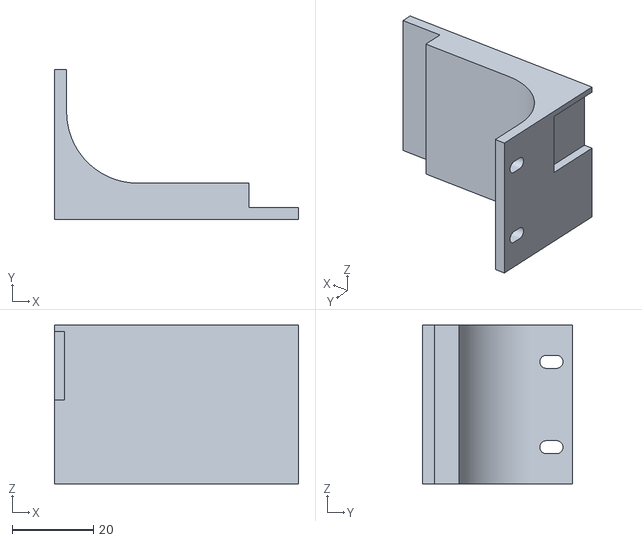
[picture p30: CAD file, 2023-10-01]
clean_nozle/dryer_vulcano.stl
60.0 x 37.0 x 39.0

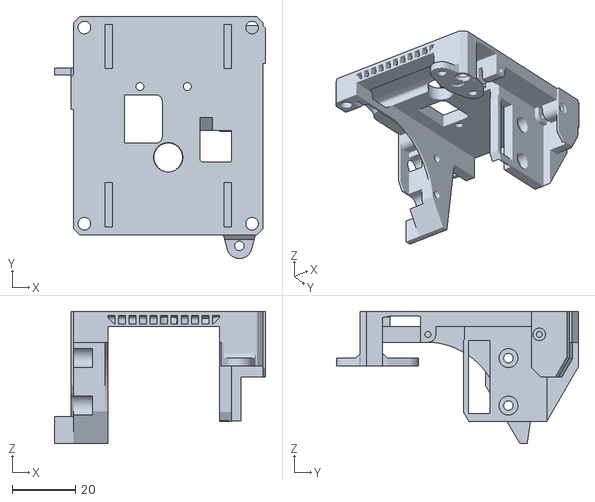
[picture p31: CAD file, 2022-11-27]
karas/Karas_niz_bltouch.stl
66.8 x 76.5 x 41.8

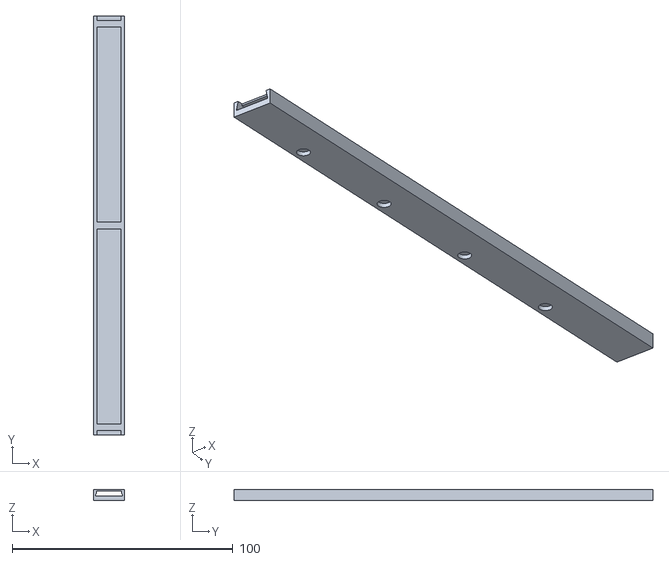
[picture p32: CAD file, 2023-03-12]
led_rgb/Led_holder.stl
14.0 x 190.0 x 5.00

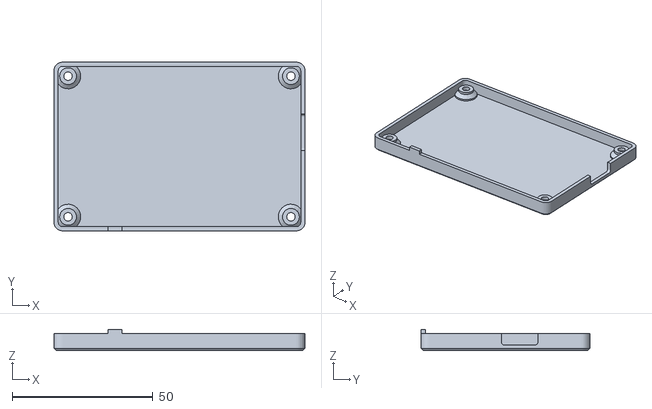
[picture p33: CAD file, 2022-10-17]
placement/case-bottom.stl
89.2 x 60.0 x 7.50

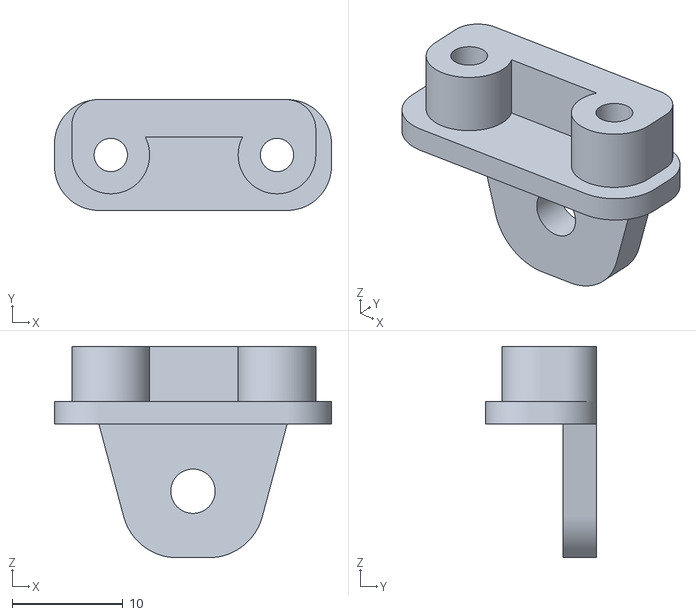
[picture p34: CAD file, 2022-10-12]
adxl345_2_mcu/adxl.stl
25.0 x 10.0 x 19.1

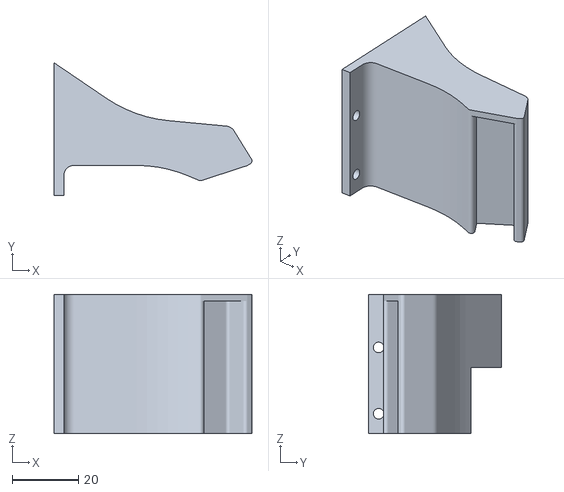
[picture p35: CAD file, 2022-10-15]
clean_nozle/shetka_3d.STL
59.7 x 40.0 x 42.0

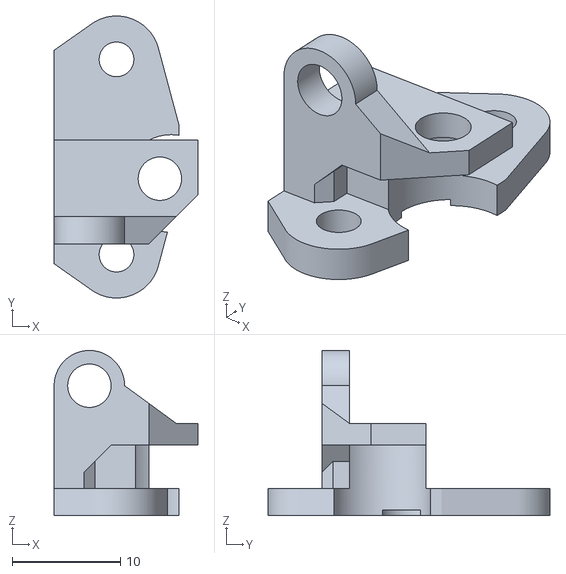
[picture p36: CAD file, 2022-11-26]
karas/BLTouch_holder.stl
13.2 x 26.0 x 15.2

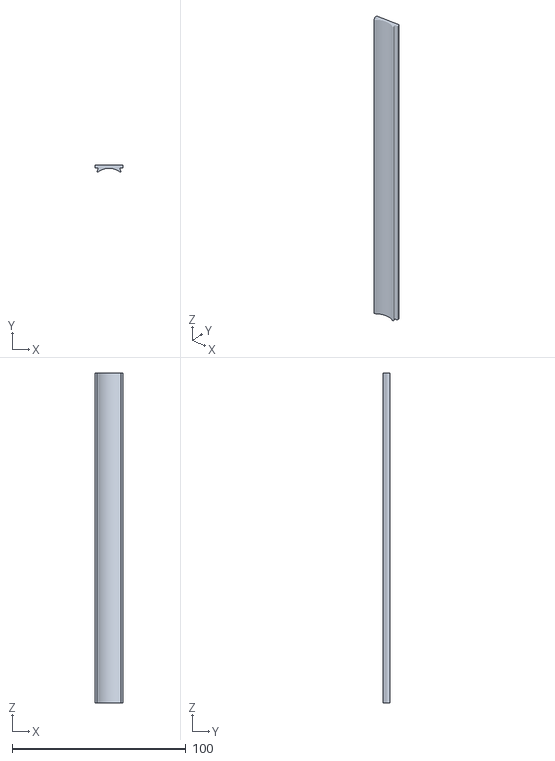
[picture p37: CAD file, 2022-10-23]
led_rgb/1_long_190mm.stl
16.0 x 3.98 x 190.0

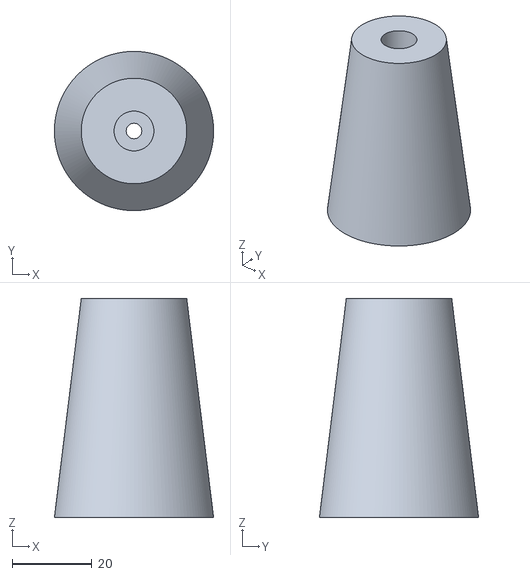
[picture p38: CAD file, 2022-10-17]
placement/stand.stl
40.0 x 40.0 x 55.0

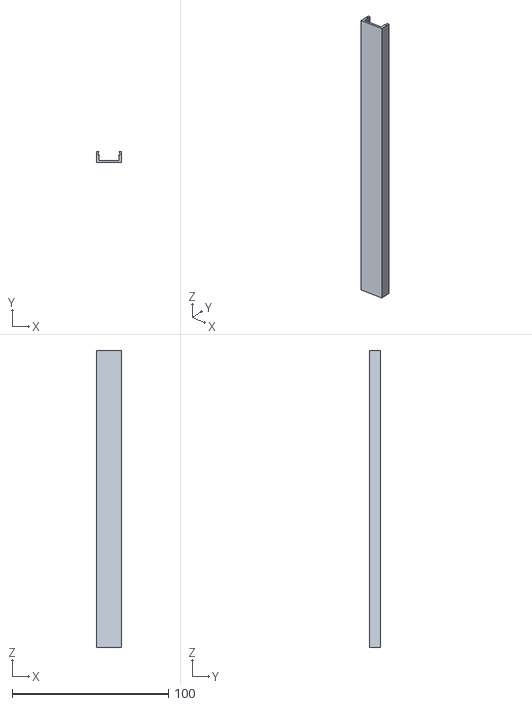
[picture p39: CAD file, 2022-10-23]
led_rgb/2_long_190mm.stl
16.0 x 7.00 x 190.0

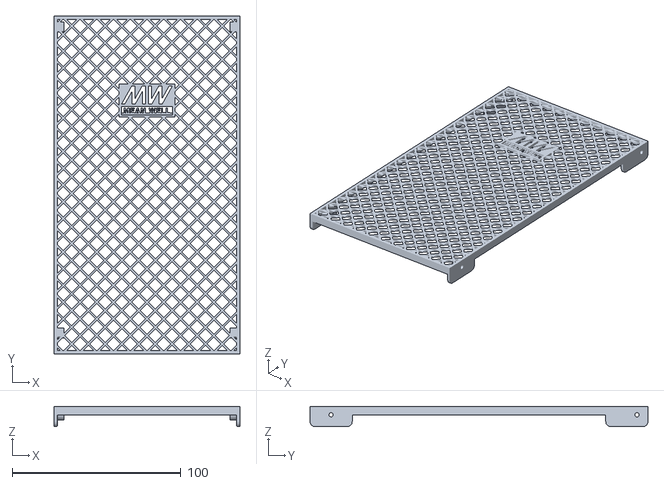
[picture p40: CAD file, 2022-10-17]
placement/Mean_Well_PSU_cover_-_fanless.stl
110.0 x 200.0 x 12.0

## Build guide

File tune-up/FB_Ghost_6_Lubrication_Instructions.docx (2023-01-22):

Много кто просил и много кто ждал инструкцию по разборке и смазке FBG6 и вот постараюсь сделать это. Сразу предупреждаю: 3д принтер я увидел впервые, своими газами пару месяцев назад. По этому на мой профессионализм расчитывать не нужно! Вы все делаете на свой страх и риск, я только расскажу и подскажу как это делал я.

Для начала, я купил бензин «Галоша», нашел тару для промывки и бумажные полотенца.

Начинаем.

ОБЯЗАТЕЛЬНО ОТКЛЮЧАЕМ ПРИНТЕР ОТ РОЗЕТКИ!!!!

Отключаем шлейф головы. Вынимаем ПТФ трубку. Вынимаем заглушки. Ослабляем фиксирующие болты. Ослабляем болты натяжки ремней. В любой момент можно открутить,снять боковые стенки. Снимаем ремни.

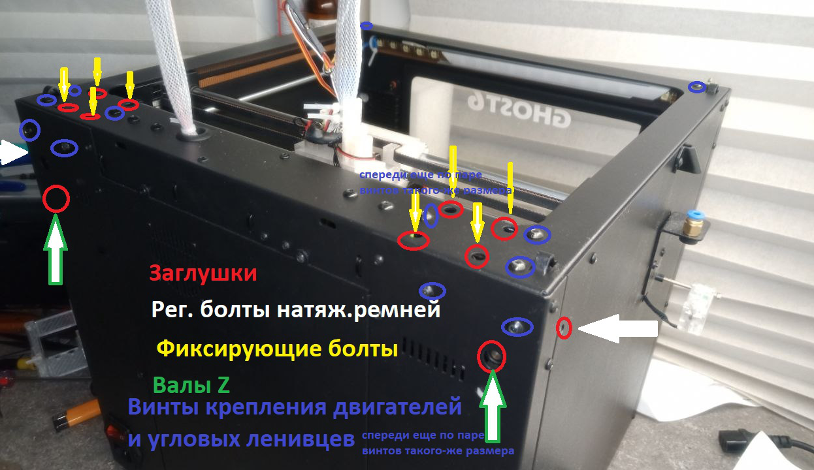
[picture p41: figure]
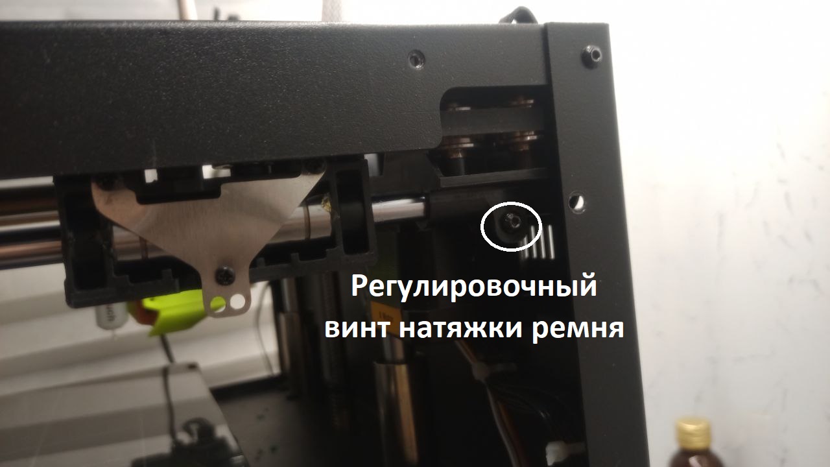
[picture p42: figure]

Фланцевые подшипники – далее по тексту «ленивцы» (я узнал, что они «фланцевые» уже после того, как написал больше половины текста)))

Пока только ослабляем винты крепления двигателей и угловых ленивцев.(

Дальше, хватаемся за валы Y и тянем/толкаем их аккуратно, но настойчиво в сторону отверстий сзади, до тех пор, пока не будет возможности снять валы Х вместе с кареткой и боковушками. Вынимаем валы до конца

Если отверстия маленькие, то просто аккуратно откручиваем большие винты креплений и все по очереди вынимаем.

Достаем линейные подшипники из каретки с помощью сверла на 8 (у меня жестко сидели в карасе) -у вас возможно легко выпадут. Из стоковой каретки, я вынимал подшипники «варварским» способом, описаным в гите у @Tom_Tomichа.

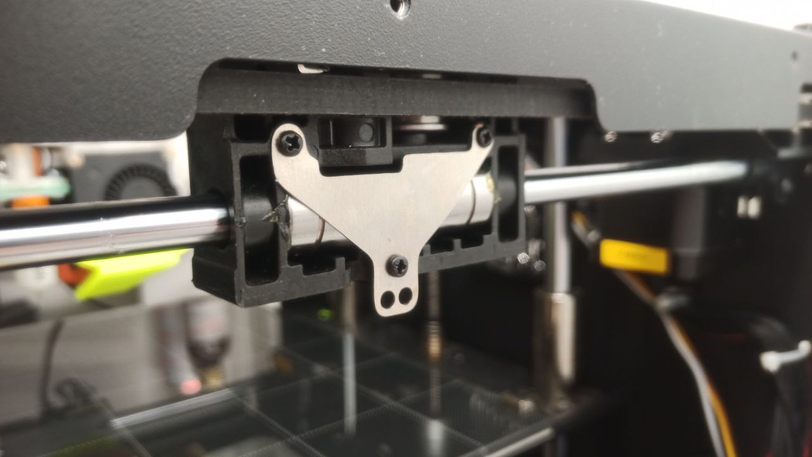
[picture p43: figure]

Подшипники из боковушек достаются откручиванием трех +винтиков на жестянке..

Сверху, на каретке есть маленькие дырочки, над осями ленивцев. – вставляем туда самый маленький шестигранник из набора и выдавливаем оси. (У меня этой фото нет, где-то в группах видел, но не нашел, в любом случае вы их увидите) иногда идет жестко – можно аккуратно постучать по ключу.

Будте внимательны, не потеряйте распорные шайбы, если они есть!!!(сверху и снизу от пар ленивцев)

Откручиваем и снимаем угловушки и крепл.движков.

На креплениях двигателей и на угловых держателях оси вынимаются с помощью болтиков М3 – вкручиваем-тянем.

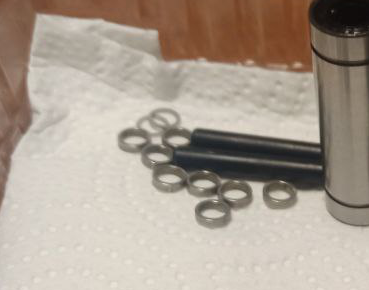
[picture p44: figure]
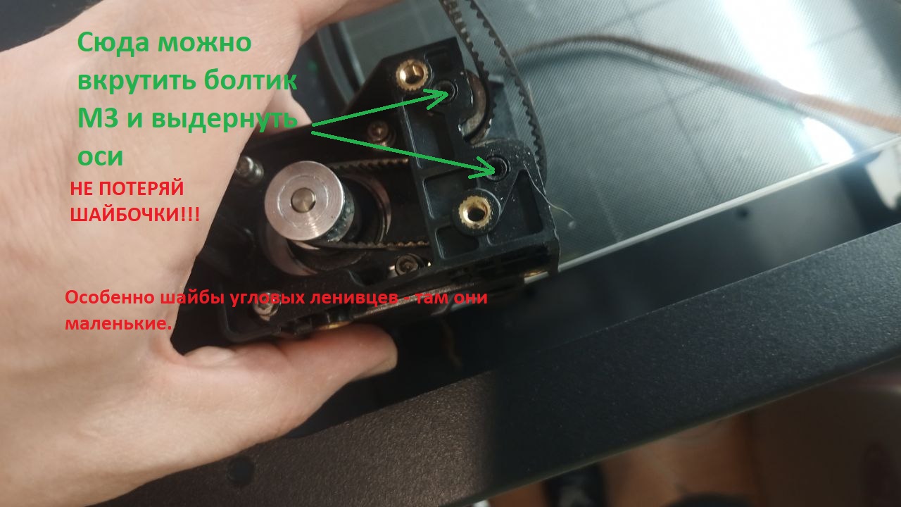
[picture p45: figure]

(Следите за шайбами. В угловых – шайбы тонкие, находятся промеж пар ленивцев. По одной на каждой угловушке)

-Тащим полоскать наши подшипники. Кодаем в тару. Заливаем Галошей и полоскаем.

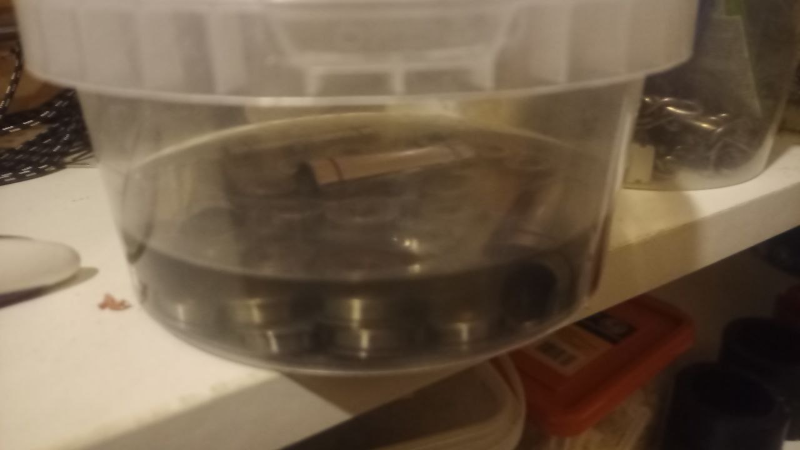
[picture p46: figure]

Полоскаем- получаем…

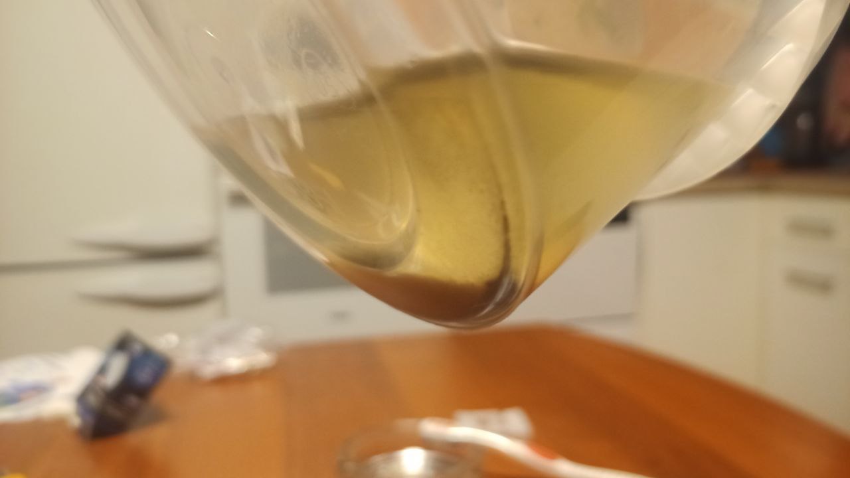
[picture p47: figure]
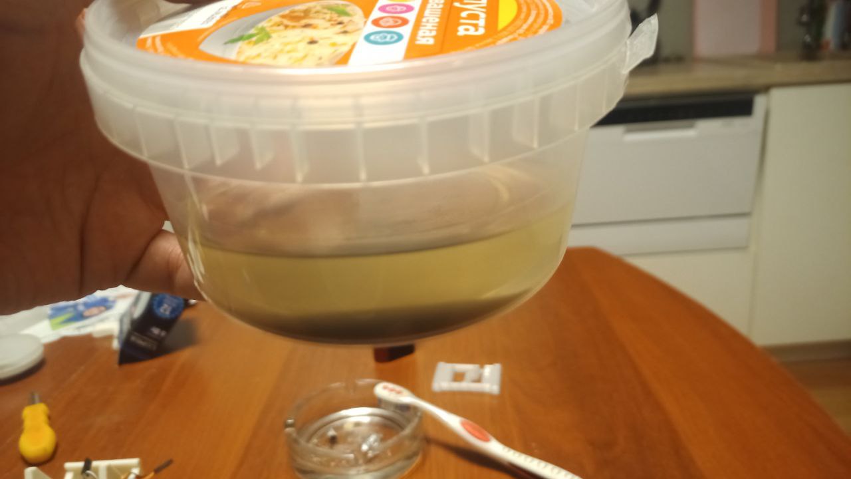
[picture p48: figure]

Дальше самое интересное.. достаем ленивца из банки, кладем на бум полотенце и препарируем…

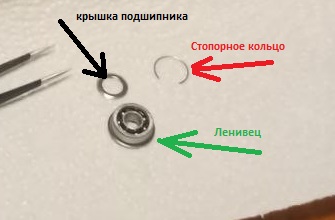
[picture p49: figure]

Поддеваем пинцетом стопорное кольцо, снимаем его и крышечку.

Потом я брал его пинцетом и полоскал в открытом состоянии.

Дальше набиваем смазкой, закрываем, протираем, убираем. И так 24 раза)

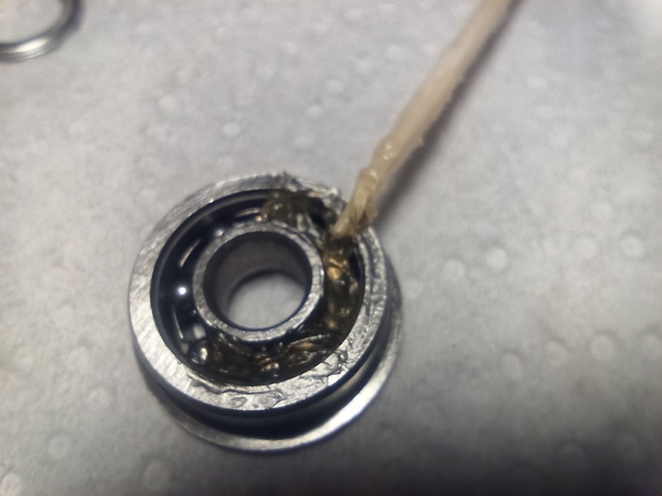
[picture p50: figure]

Линейные подшипники набиваем смазкой и с двух сторон, одновременно вставляем валы и сдавливаем их. (фото -нет)

Дальше, возвращаемся к принтеру и возвращаем все туда, откуда достали)

Тут, у кого отверстия маленькие – могут рассверлить отверстия под валы Y до ~10мм

Собрать всё взад -не сильно сложнее. На вставляем оси ленивцев чуть меньше середины, надеваем шайбу,ленивца , чуть проталкиваем ось потом второго ленивца, вставляем оставшуюся шайбу и поправляя пальцем, задвигаем ось до конца. На угловых – первая пара ленивцев, шайбошка, вторая пара..

Схема ремней:

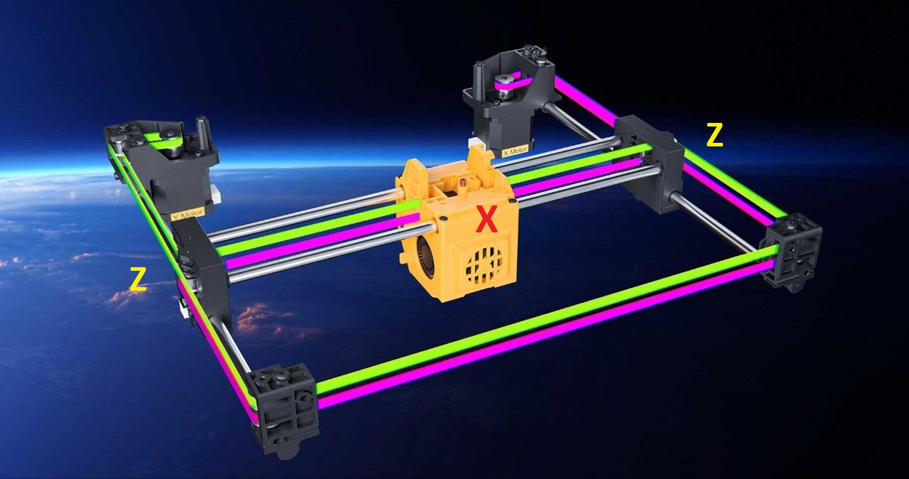
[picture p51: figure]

Вставляем ремень в держатель движка.. подвешиваем его на один-два болта

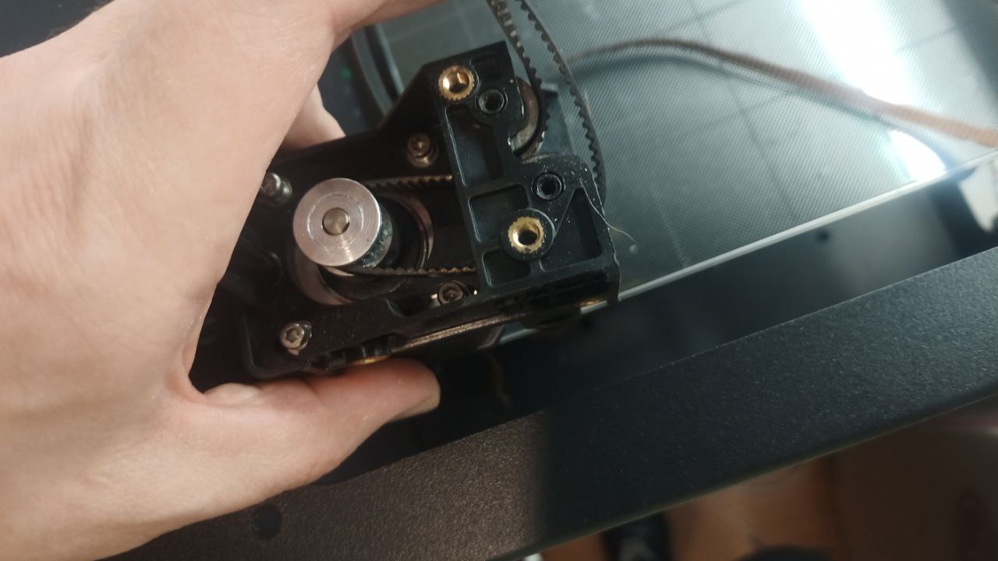
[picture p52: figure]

Тянем ремни через оба уголка, потом мотор с другой стороны. Уголки подвешиваем после протяжки обоих ремней через них. (там еще будет провод люстры мешать – его как-то отсоединить с платы или протянуть за ним). Наживляем остальные винтики крепежа.

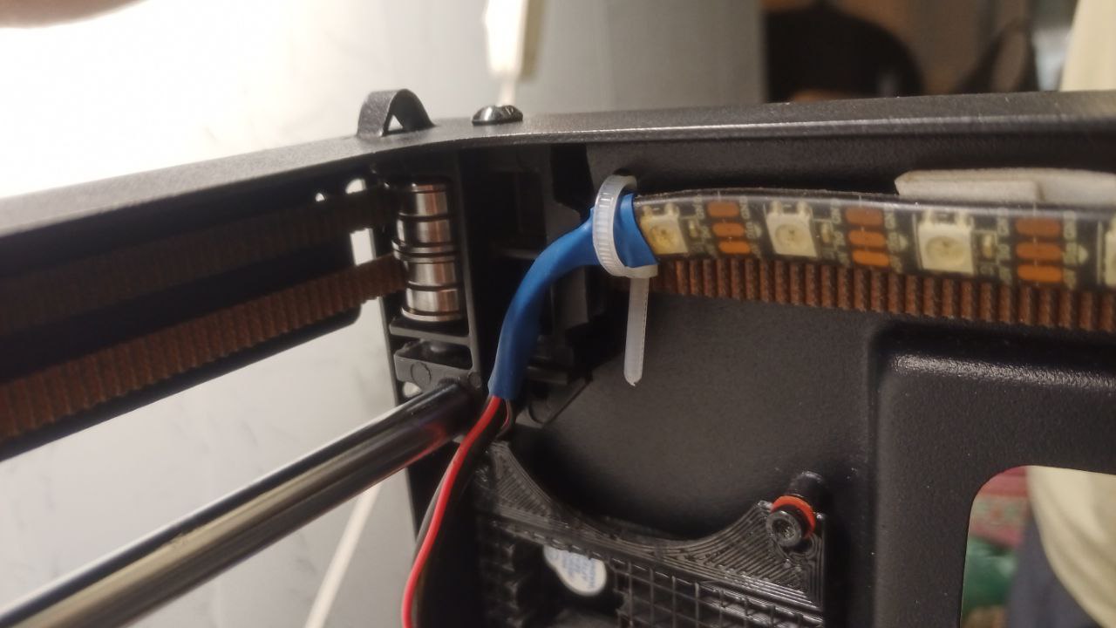
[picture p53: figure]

Далее вставляем Y-валы сначала до половины, возвращаем лин. подшипники в Х-каретки, каретки вешаем с валами и подшипниками головы на Y, и задвигаем Y до конца на место. Вешаем голову на подшипники, если она вешается сверху (если подшипники вставляются в голову сбоку - тогда она уже должна была висеть в момент установки подшипников на валы Х )). Дергаем за голову – проверяем, что нигде не закусывает ничего. Затягиваем винты креплений.

Каретки ставим напротив вырезов в раме (см фото №3) , продеваем ремни и цепляем равномерно за голову. Поправляем ремешки, проверяем что они на своих местах, снова катаем руками за голову. (тут можно натянуть ремни вручную, как можно сильнее, и примерно равномерно), потом натягиваем ремни уже окончательно, по другой инструкции (но лучше, наверно, сначала вернуть боковые стенки на место). Собираем голову в кучу, подключаем и всё.

Про Z подшипники - в этот раз я их не снимал, там еще легче, но про это я, или кто-то другой дополнит позже..

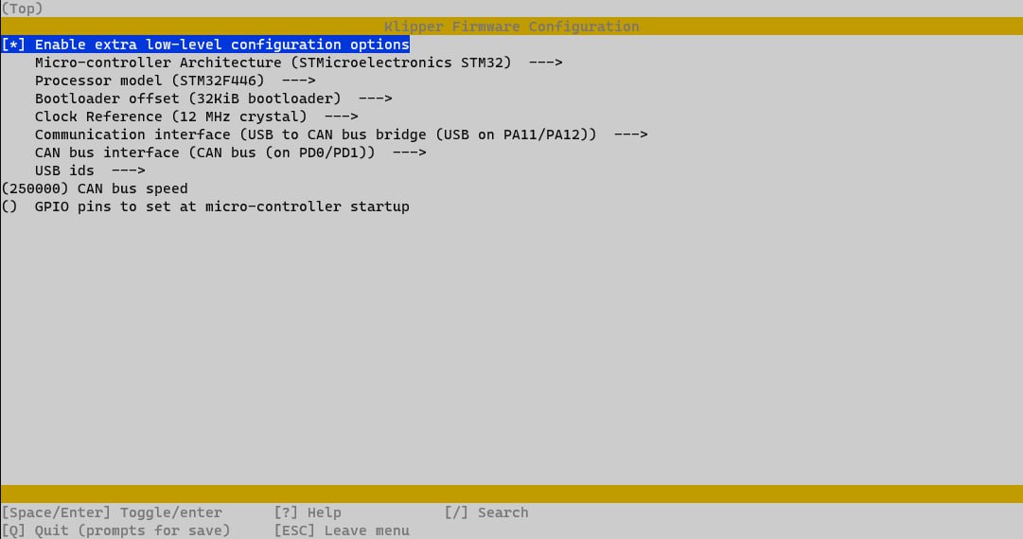
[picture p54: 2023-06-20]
tune-up/ebb_can/make1.jpg

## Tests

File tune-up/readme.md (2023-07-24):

*<h2>Мануалы по настройке</h2>* 

[**Руководство на русском языке**](../FlyingBear_Ghost_6_RU.pdf) ну вдруг кто книжечку потерял.

[**Перед первым включением**](https://fb-waiters.bibirevo.net/forbeginners/justreceived)

[**Настройка ремней**](belts.md)

[**Замена сопла\кубика\термобарьера**](https://fb-waiters.bibirevo.net/hardware/fbg6/bimetall)

[**Настройка стола**](https://fb-waiters.bibirevo.net/forbeginners/heaterbedsetup)

[**Выравнивание стола и калибровка первого слоя**](https://telegra.ph/Vyravnivanie-stola-i-kalibrovka-pervogo-sloya-12-11)

[**Смазка принтера**](https://fb-waiters.bibirevo.net/tuning/oil)

[**Смазка принтера Ghost6**](FB_Ghost_6_Lubrication_Instructions.docx) в картинках  файл word

[**Инструкция по полной разборке-сборке-смазке принтера ghost 6**](https://fb-waiters.bibirevo.net/hardware/fbg6/razbor)

[**Настройка bl-touch**](../bltouch/readme.md)

[**Настройка Шагов экструдера на примере BIQU H2**](extruder.md)

[**Настройка веб камеры(Яркость, баланс и тд)**](https://telegra.ph/Nastrojka-veb-kameryYArkost-balans-i-td-04-01)

[**Регулировка тока экструдера**](potenciometr.md)

[**Смена картинки стола в Cura**](cura.md)

[**Подключение и настройка EBB Can к плате BTT Octopus v1.1 \ Pro и аналогичным с встроенной Can шиной.**](/tune-up/ebb_can/readme.md)

[**Полезности для диагностики и ремонта платы MKS Robin Nano4**](plate.md)

Схема подключения  косы головы принтера
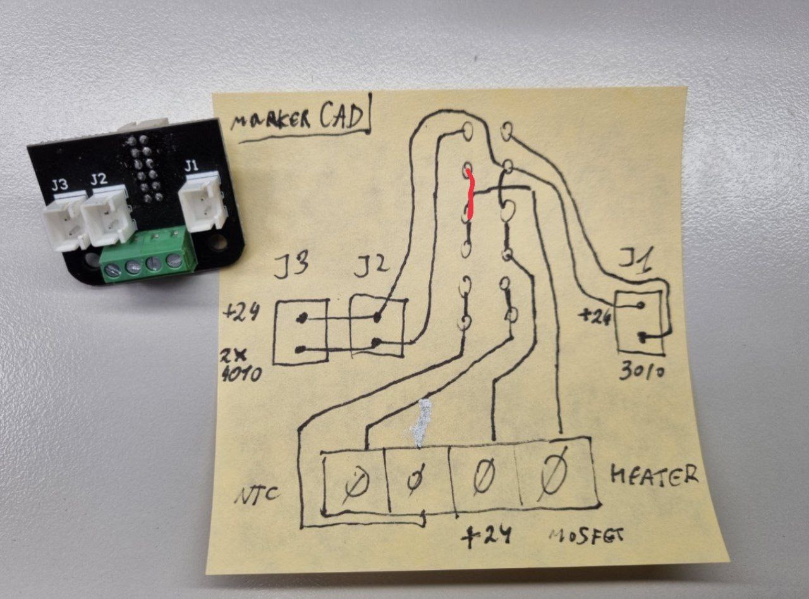
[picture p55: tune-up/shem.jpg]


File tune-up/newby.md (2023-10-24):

Пособие новичку.

Привет тебе юный падаван, поздравляю с покупкой твоего Ghost 6.  Тут мы разберем твои первые шаги с твоим новым принтером и постараемся чтобы твоя голова не взорвалась от новых знаний и ты не сделал ошибок ну или хотя бы сделал их как можно меньше.

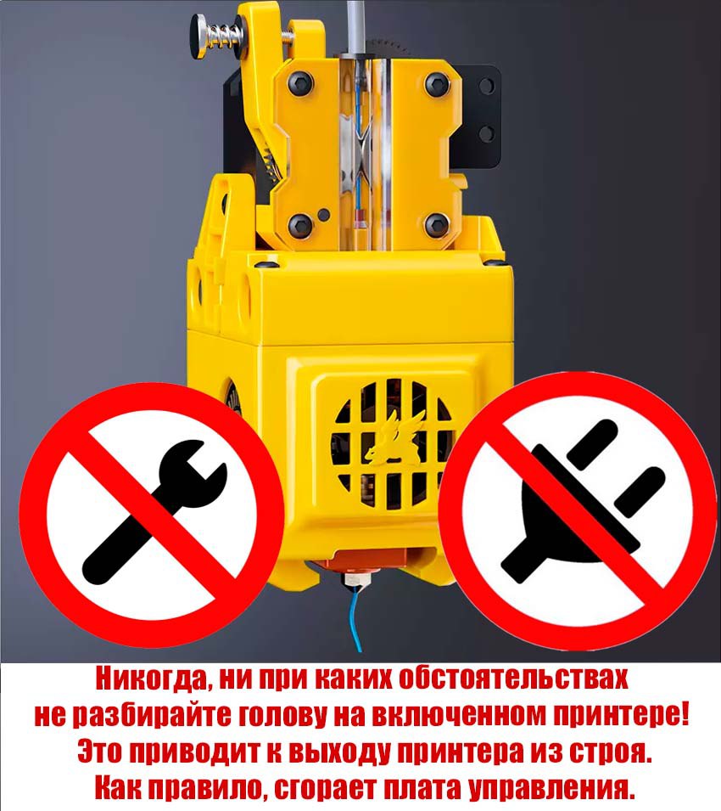
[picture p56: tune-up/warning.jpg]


1. собирать принтер по инструкции в случае нашего принтера можно и по книжке и по видео от летающих медведей, там достаточно просто и думаю дополнительных сложностей не возникнет. 
2. печать тестовой модели - это важно для проверки работоспособности принтера, выявления заводских недочетов и пока ты не вносил изменения в принтер легко открыть спор с продавцом. в общении с ним очень часто просят "Number" толи продажи толи еще как только его не переведут. это наклейка взади принтера. смело используй фото наклейки в сообщениях. 
3. при печати обрати внимание чтобы не было скрипов посторонних. обрати внимание на экран, он не должен моргать, хотя отзывчивостью родной экран не страдает но кнопки должны нажиматься там где они расположены. после печати аккуратно коснись мотора экструдера. если он как кипяток то поздравляю. тебе есть куда приложить руки. теперь тебе предстоит открутить правую боковую крышку закрепленную на 10 болтов и вытянуть крышку вниз чтобы добраться до отсека электроники. вооружится мультиметром и начать изучать [**этот мануал**](potenciometr.md)
4. После регулировок  если все ранее прошло удачно ты можешь нарезать пару своих моделей в слайсере. мои рекомендации это CURA или PRUSA (не забудь вставить стартовый и конечный коды в свойствах принтера.). совет: не гонись за скоростью. 60 мм\сек вполне нормально для стокового состояния принтера. отпечатай пару дней, не меняя настроек внутри принтера.  Данная рекомендация для того чтобы выявить родные болячки чтобы можно было с честным лицом общаться с продавцом в случае каких либо проблем с железом.  если они появятся то вероятнее всего для этого хватит 10-15 часов печати. не волнуйся почти все их можно решить самостоятельно, но ведь хочется и бесплатно)  поэтому не бойся в случае проблем писать продавцу и прикладывать фото.
5. поменять (или хотя бы проверить) тефлоновую трубку в термобарьере, с завода она может быть короче чем надо, в результате пластик начинает выдавливать ее вверх, образую внизу пробку, которую мотор экструдера не в состоянии продавить (характерный признак - щелчки в экструдере как будто происходят откаты и рваный пластик на моделе). У трубки не должно быть возможности двигаться вверх или вниз при установленном моторе экструдера. Начать можно с трубки, которая длиннее штатной на 1 сантиметр, постепенно подрезаяя ее и пытаясь усадить мотор экструдера на место (чтобы винты входили в боковые отверстия), допустимо небольшое усилие (преднатяг, так сказать), но не слишком большое, чтобы трубка сама по себе не замялась. Подходит любая стандартная из ближайшего магазина с 3д принтерами. Отрезать строго перпендикулярно, стараясь не деформировать форму канала.
6. для того чтобы начать печатать необходимо откалибровать размер откатов. на стоковом они огромные и примерные значения это где то 2 мм +- но откалибровать не помешает. сделать это лучше [тут](https://k3d.tech/calibrations/retractions/) или [тут](http://retractioncalibration.com/)
7. вероятнее всего именно в эти дни ты увидишь такую надпись на экране:
   
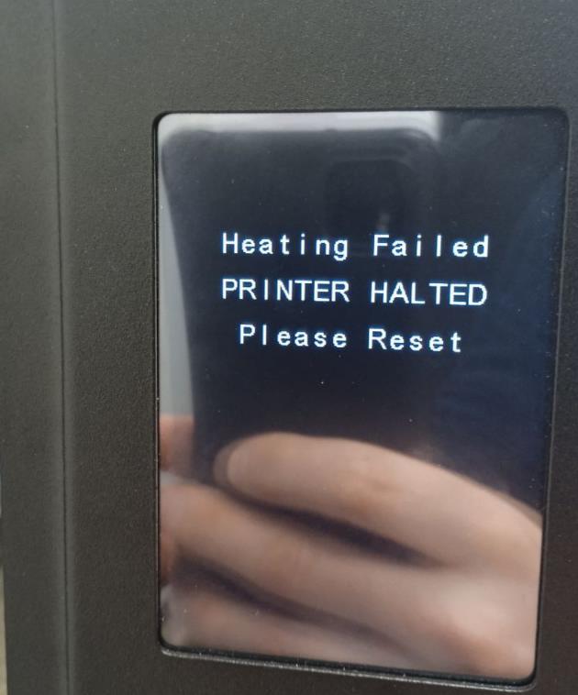
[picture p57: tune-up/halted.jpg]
   

 не пугайся, у тебя просто умер термистор так как он самое слабое место в комплектации нашего принтера. теперь тебе предстоит освоить следующее умение - разбор головы фидера и термистора. очень советую перд этим прочитать раздел [**Что купить**](../what_2_buy/readme.md) и инструкцию по сборке и разборке головы [тут](https://fb-waiters.bibirevo.net/hardware/fbg6/bimetall)

7. после замены термистора, а общая рекомендация это не брать тот же самый, а купить и поставить 3950 100к  и горло биметалл которое позволит уменьшить откаты, теперь нам необходимо поставить прошивку получше того стокового недоразумения от медведей.  идем [сюда](../marlin/readme.md) или сюда(Гит паши). качаем устанавливаем по инструкции  делаем PID ехтрудера PID  стола. калибруем откаты тут](https://k3d.tech/calibrations/retractions/) и настраиваем LA [тут](https://k3d.tech/calibrations/la/) 
8. если ты молод душой и хочешь пользоваться всеми возможностями принтера которые можно получить в 21 веке то тебя ждет увлекательная установка клиппера. на данный момент для этого не надо быть супер умным, достаточно просто повторять инструкции которые написаны на русском мной). ничего сложного нет, хотя понадобятся небольшие финансовые траты. в разделе [**Что купить**](../what_2_buy/readme.md) ты найдешь подробный список комплектующих и не забудь купить акселерометр это необходимо для продвинутого алгоритма Input shaping который улучшит твое качество печати и скорость.  если ты не хочешь ставить клиппер а воспользоваться алгоритмом очень хочется то можно его попробовать настроить вручную. для этого советую посмотреть видео от Дмитрия Соркина [вот это](https://www.youtube.com/watch?v=ZFPkfZEB-XU) хотя оно для клиппера  найду для марлина - вставлю.
9.  Конечно мой совет будет переходить на клиппер. и этот гит с модификациями этому подтверждение, почитай статьи просто как художественную литературу, в будущем это поможет тебе избрать направления модификаций, найти нужные именно тебе, принять взвешенное решение и оценить обьем работы. не торопись прочитав одну статью. к результатам можно прийти несколькоми путями и на данном гите есть разделы которые предоставят ьебе их если не все, то несколько возможных.

10. Руководство по устранению неполадок качества печати посмотреть можно [тут](https://www.simplify3d.com/resources/print-quality-troubleshooting/)

11. Про датчик огня. в штатной прошивке для сработки надо выполнить 2 условия, температура хотенда выше 270 и засветка датчика. если в переводе на человеческий " пожар был потушен путем полного выгорания" ))) поэтому не стоит класть  тлеющую бумагу в принтер для проверки сработки и свечки ставить туда же, как и надеятся что если что принтер разберется сам. контроль за принтером нужен, и огнетушитель даже если он никогда в жизни не понадобиться стоит купить. 

Удачи тебе на пути к совершенству юный падаван!

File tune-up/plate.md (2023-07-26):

**Полезности для диагностики и ремонта платы MKS Robin Nano4**

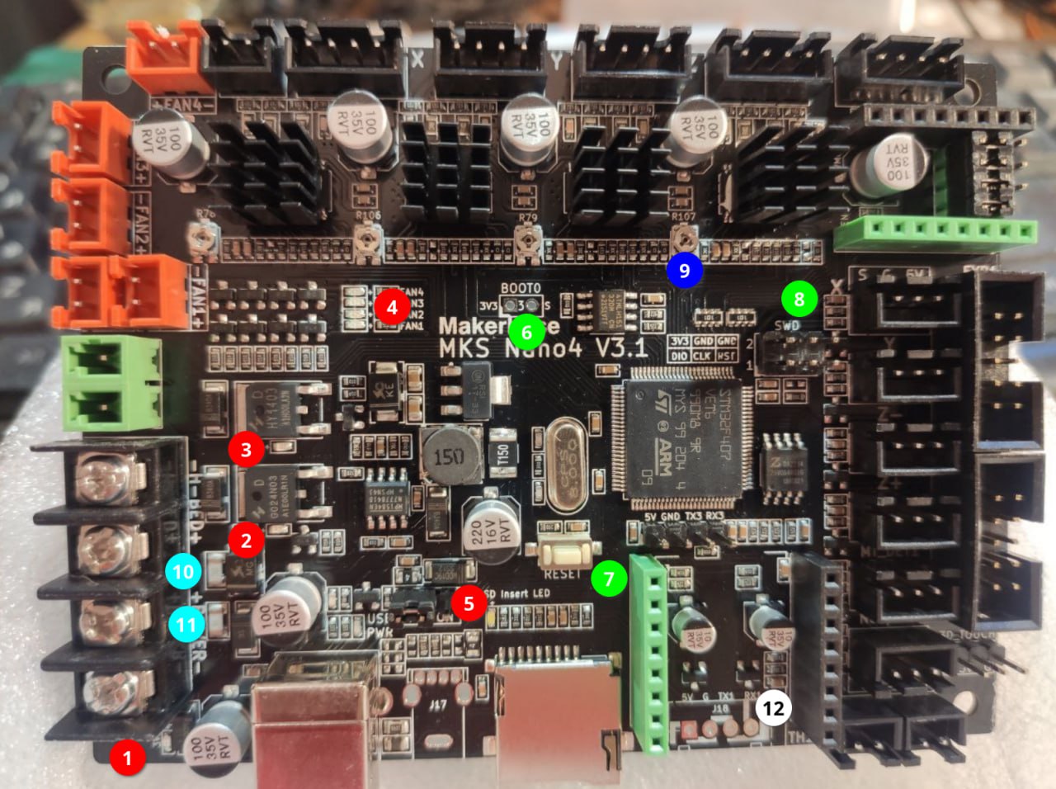
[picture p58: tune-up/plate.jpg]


1. Светодиод "3.3В" - наличие питания процессора. В норме светится ярко при питании платы от 12/24В БП или от USB (при установленном джампере USBPWR)

2,3. Светодиоды "Нагрев стола(2)" и "Нагрев экструдера(3). Зажигаются при активации соответствующего канала нагрева, при установившейся температуре мигают. Включены параллельно соответствующим выходным клеммам. Если светодиод горит, но нагрева нет, проблема в проводке или нагревателе.

4. Светодиоды "FAN1-FAN4". Аналогично каналам нагревателей.

5. Джампер USBPWR. Питание процессора от шины USB. При нормальной работе находится в положении OFF. Рекомендуется ставить в ON при прошивке платы вне принтера, записи bootloader, и диагностике процессора.

5-S. Светодиод "SD" справа от джамера USBPWR. Загорается при вставленной карте microSD в слот считывателя (и наличии питания 3.3В). Единственный белый светодиод на плате.

6. Джампер BOOT0. Запуск загрузчика DFU процессора STM32. В большинстве плат Nano4 с завода не распаян. Используется для загрузки mks-bootloader и прошивки в чистый (свежезапаянный) процессор, а также на последнем этапе диагностики  процессора на работоспособность. Исправный процессор при замкнутом джампере после включения или RESET должен определяться на шине USB как STM32 in DFU mode. Рекомендуется использовать с включённым USBPWR.

7. Кнопка RESET. Перезапуск процессора. Удобно применять совместно с джампером DFU или при перепрошивке процессора с карты microSD.

8. Разъём программирования SWD. Пригодится разработчикам прошивок, а также как альтернативный способ записи загрузчика mks. 

9. Переменный резистор установки тока мотора экструдера. Для стоковой головы рекомендуется выставить опорное напряжение 0.6-0.7В, что китайцы ленятся настраивать. Напряжение может быть выставлено только при подаче на плату силового питания.
Ориентировочно должен стоять в положении "01:30". С завода - в положении "12:00" (см. фото)

10. Предохранитель 30А в цепи нагревателя стола. Включён между плюсовой клеммой БП и плюсовой клеммой нагревателя.

11. Предохранитель 15А в цепи нагревателя экструдера. Включён между плюсовой клеммой БП и плюсовой клеммой нагревателя. Также через этот предохранитель запитаны вентиляторы, драйверы всех моторов И схема питания ПРОЦЕССОРА (через цепочку понижающих стабилизаторов 24В->5В->3.3В)

12. Разъём UART1. Дублирует контакты в "кроватке" от модуля WiFi. Эстеты, по разным причинам не желающие использовать перемычки DUPONT MALE-FEMALE, могут распаять самостоятельно разъём XH2.54 или PLS04.

**НАПОМИНАНИЕ!**

Тем, кто перебирает косу, меняет плату Nano4 на Nano3, ставит внешний мосфет для управления нагревом экструдера, а также занимается иными улучшениями:

Необходимо соблюдать полярность подключения проводов нагревателя - красный к плюсу разъёма на плате, чёрный к минусу! 

Звучит диковато (сам по себе нагревательный картридж неполярный), но на плюсовой шине нагревателя также сидят вентиляторы (китайцы экономные, на 2 провода в косе пожмотились)

Мне уже пару раз в личке задавали вопрос по поводу того, почему вентиляторы выключаются при включении нагрева )))

Несоблюдение полярности подключения приведёт к странностям в логике управления нагревателем и вентиляторами. Также возможно повреждение мосфетов управления вентиляторами и процессора (я ранее описывал диодную "защиту").

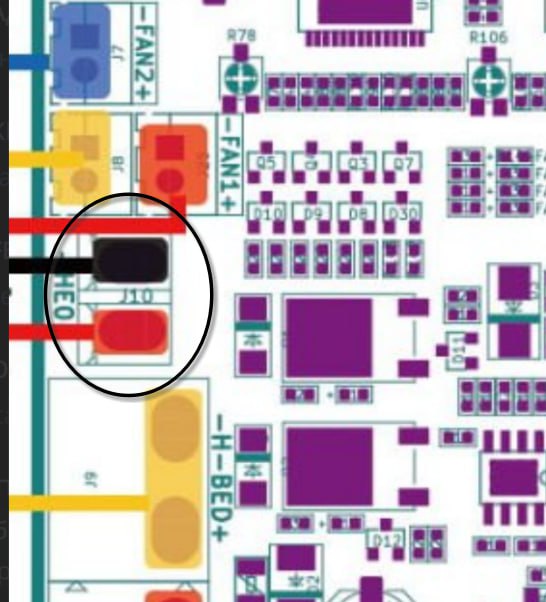
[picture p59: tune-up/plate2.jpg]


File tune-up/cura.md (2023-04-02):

 как в куре менять картинку стола..
1) Файл png кладем в Program Files\UltiMaker Cura 5.3.0\share\cura\resources\images
2) Файл obj кладем в Program Files\UltiMaker Cura 5.3.0\share\cura\resources\meshes
3) В профиле (Профили находятся в Program Files\UltiMaker Cura 5.3.0\share\cura\resources\definitions) из которого делали принтер при первой настройке (Если "Custom FFF printer" то это файл custom.def.json) добавляем\меняем две строки

"platform": "имя файла.obj",
"platform_texture": "имя файла.PNG",

[скачать файлы](FBG6_Table.rar)

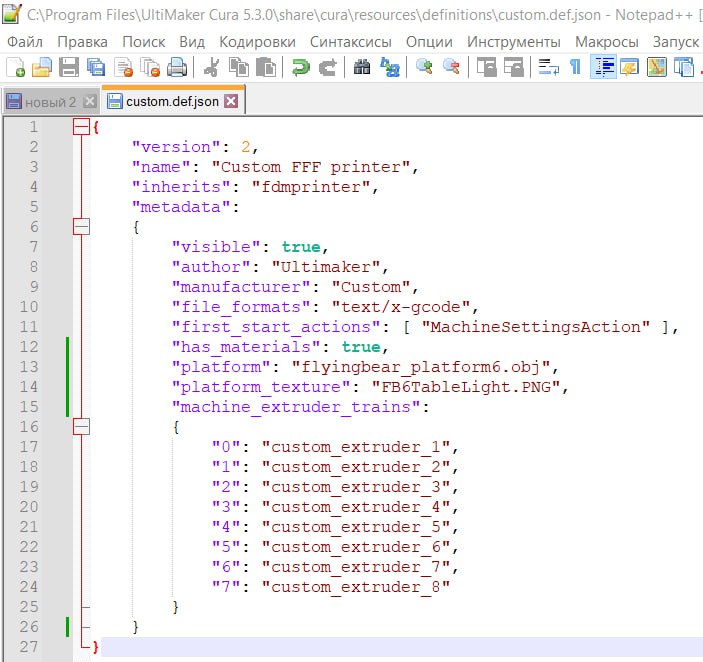
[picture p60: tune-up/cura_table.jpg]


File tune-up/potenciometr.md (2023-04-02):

**Регулировка тока экструдера**

На многих принтерах FBG6 из обновлённой партии (где пищалка-пожарный оповещатель переехала с лицевой панели принтера в камеру печати) наблюдается повышенный ток двигателя экструдера. Это проявляется в повышенном нагреве мотора, из-за чего PLA в зубьях фидера как ириска вязнет. Также есть риск перегрева мотора и пропуска шагов.

Рекомендуется снижение опорного напряжения драйвера шагового двигателя переменным резистором R107 до величины 0.6-0.8В. 

Питание принтера  осуществляется от сети 220В, запитывать от USB недостаточно Поизучав схемотехнику стоковой платы MKS Robin Nano4, на ней опорные напряжения VREF (устанавливаемые переменными резисторами) формируется от внутреннего стабилизатора в каждом драйвере, а не от системной шины +5V (питание от шины 5В - типовое решение для сменных драйверов). 
Поскольку внутренний источник в драйвере формирует 5В из силового напряжения +24В,  для настройки VREF на стоковую плату нужно подать эти самые +24В, получаемые от силового источника питания принтера. 
**Другими словами, питания от USB недостаточно, требуется включать принтер в сеть 220В**

ВНИМАНИЕ! В процессе настройки принтер находится под сетевым напряжением 220В. Мультиметром лезть крайне аккуратно, первые 2 клеммы на блоке питания под сетевым напряжением (красный и чёрный провода, китайская схема маркировки фазы и нуля)

Для уменьшения напряжения ротор резистора крутить по часовой стрелке.  

При подстройке напряжение контролировать мультиметром.  "Минус" мультиметра подключить к минусу блока питания или платы принтера,
плюсовым щупом коснуться ротора R107 и проверить напряжение. Крутить крайне аккуратно! буквально по градусу. настройка очень резкая и крутнув много вы можете вывести драйвер из строя!

фото: 

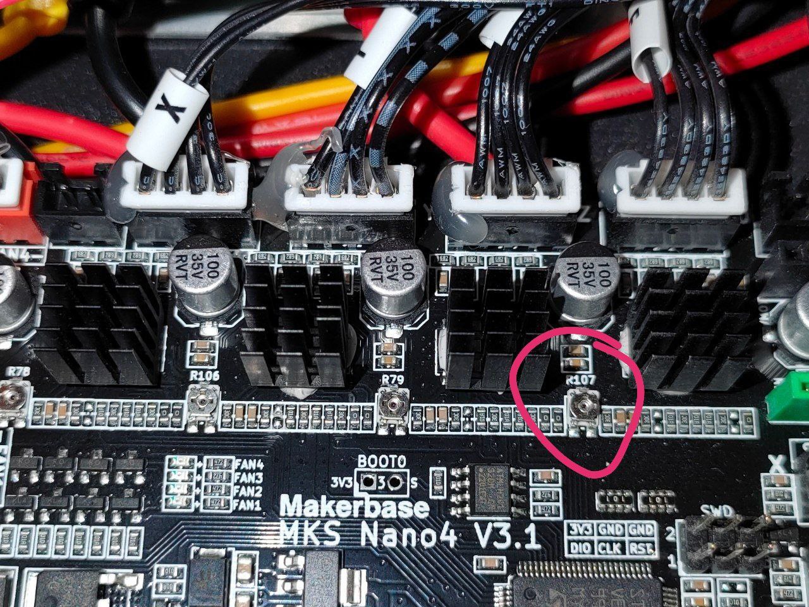
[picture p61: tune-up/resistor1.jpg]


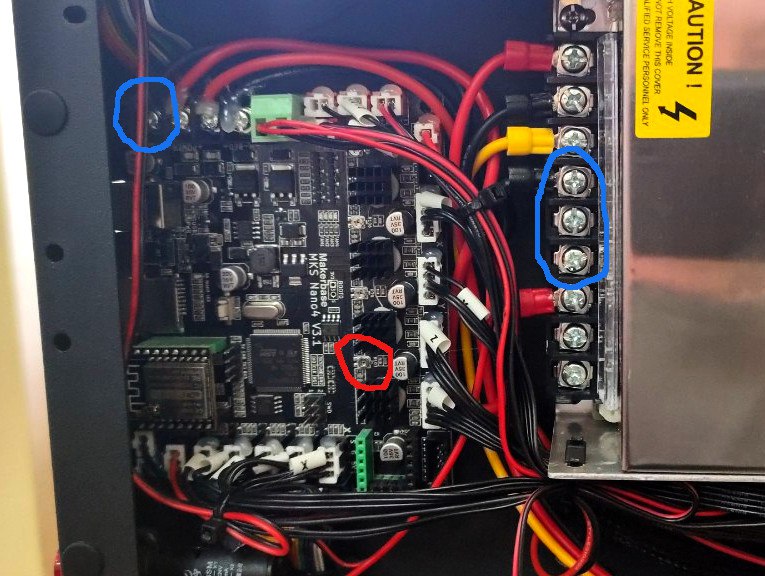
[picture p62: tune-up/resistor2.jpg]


см. официальное видео от медведей https://www.youtube.com/watch?v=mrw70FVJ_q0

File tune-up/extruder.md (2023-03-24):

**Настройки шагов экструдера на примере BIQU H2**

после того как все подключили настала пора настроить klipper
1. В `printer.cfg` в раздел `[extruder]` добавим строку `min_extrude_temp: 0`  - это позволит выдавливать пруток без включения нагревателя. Строка временная, потом можно удалить.
2. `rotation_distance: 3.4334` это моё значение можно использовать как отправную точку для расчетов. `microsteps: 16` У меня 16  если у вас другое, не жалуйтесь что цифры не совпадают).
3. Откручиваем кулер правый, под ним у нас зажим горла. ослабляем нагреватель и термистор  и снимаем хотблок вместе с горлом.если лень или вы еще не зажимали сопло на горячую можете открутить сопло.
4. заправляем пруток, так чтобы он вышел наружу снизу и откусываем его вровень с корпусом.
5. В консоли пишем 
```
G91

G1 E300 F60
```
Это выдавит 300 мм прутка на обычной скорости экструдера.(такой расчет достаточно точный и рекомендуемый но у меня нет под руками инструмента такой величины, я решил для себя поставить 150 и мерял штангелем.)

6. *Беру свой rotation_distance = 3.4334 и делю на 300 (столько я отправил прутка на продавливание) 
получаю Х и это число умножаю на фактически вылезший пруток.* Такой нехитрой формулой получаем свой rotation_distance идеальный именно для вас.

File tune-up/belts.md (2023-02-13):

**Порядок настройки ремней**

1. Предварительно отрегулировать по ощущениям, звуку или напечатанным заранее  измерителю натяжения [модель тут](https://www.thingiverse.com/thing:2923242)
   
2. Важно что-бы ремень не был недотянут или перетянут. Движение головы при перемещении рукой должно быть достаточно плавным, без рывков. 
   
3. При равномерном натяжении обоих ремней направляющие по оси X будут перпендикулярны направляющим по оси Y. Проконтролировать это можно замерив расстояние от горизонтальны кареток до элементов крепления направляющих. Расстояние должно быть одинаковым.

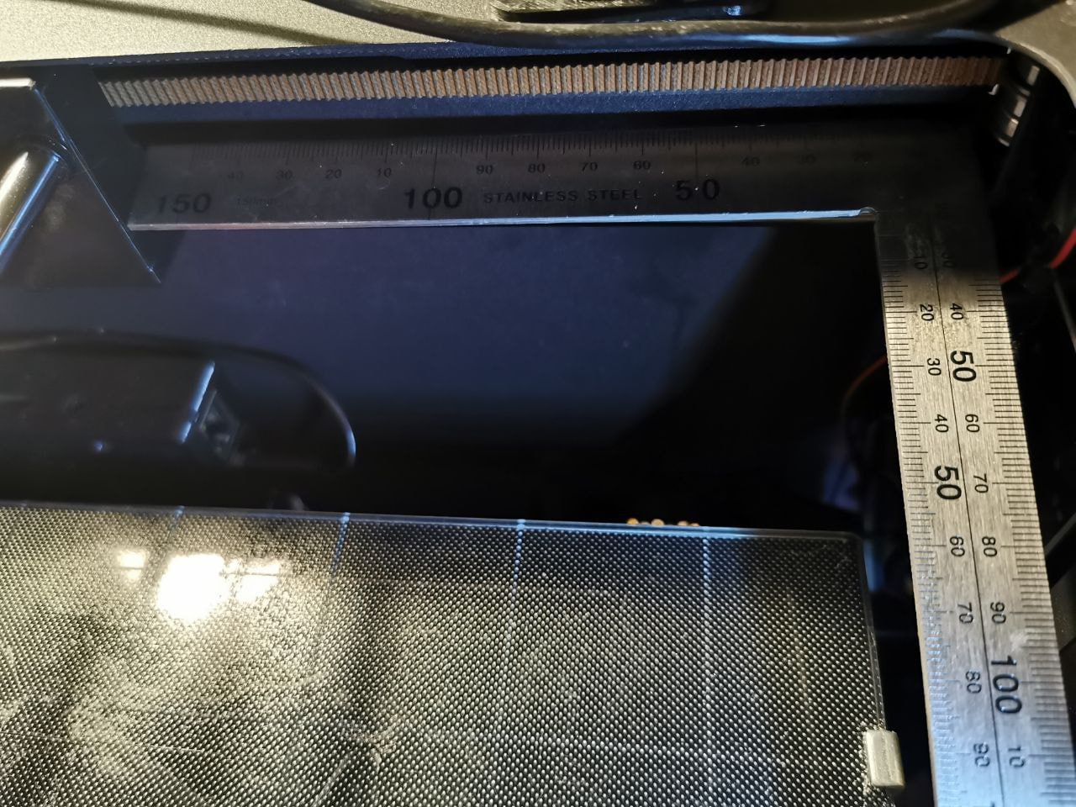
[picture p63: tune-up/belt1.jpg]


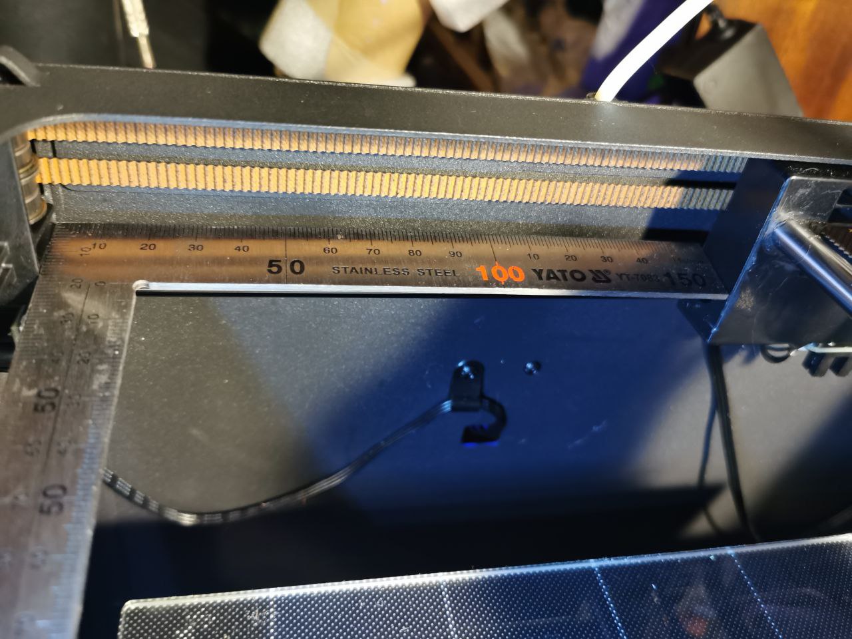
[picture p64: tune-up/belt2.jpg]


4. Важно: натяжение ремней взаимозависимо. Т.е. при натяжении ремня на двигателе X, натяжение ремня на двигателе Y тоже будет увеличиваться. Важно не перетянуть ремни на этом этапе.Каждой итерацией желательно немного затягивать один из ремней и ослаблять натяжение второго. 
   
5. Важно: геометрия принтере такова, что вращение одного из двигателей X и Y обеспечивает движение печатающей головы по одной из диагоналей. По этому легкость и равномерность движения проще тестировать двигая голову по диагонали, а не вдоль осей X или Y. 
   
   Автор @Misago7
   
   

Напечатайте квадрат в один слой(можно просто несколько периметров) и замерьте диагонали. по картинке выше будет понятно какой ремень надо отпустить\подтянуть.

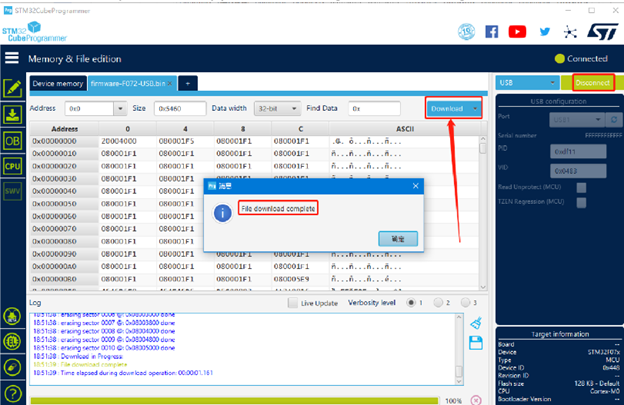
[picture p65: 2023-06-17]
tune-up/ebb_can/STMP3.png

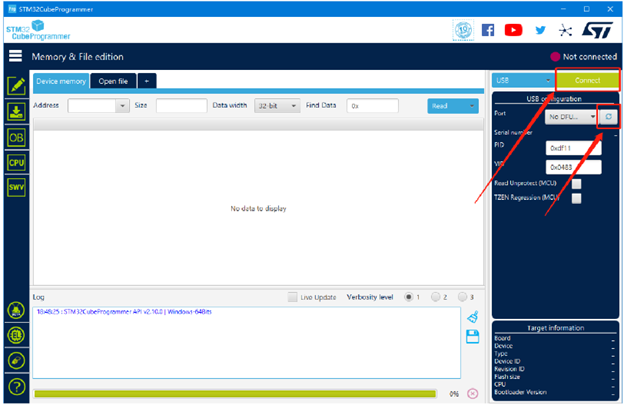
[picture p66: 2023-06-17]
tune-up/ebb_can/STMP1.png

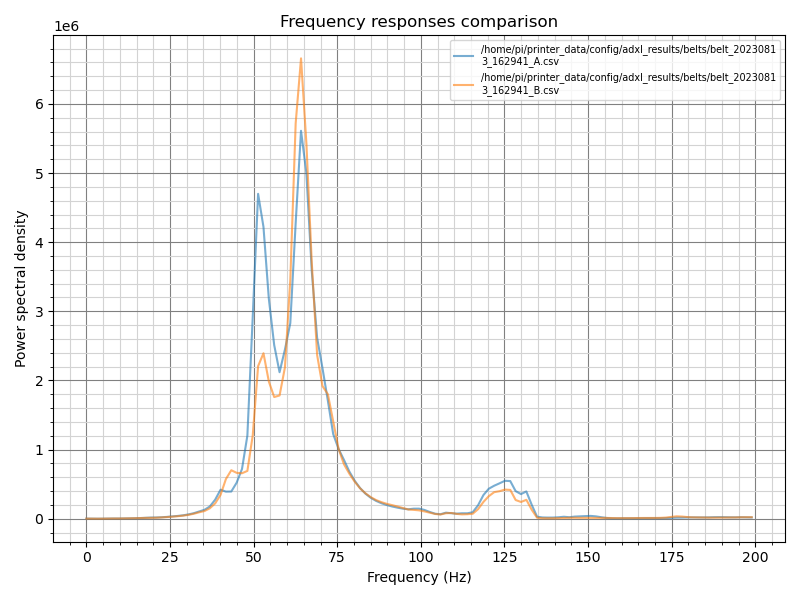
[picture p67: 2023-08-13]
klipper_config_my/adxl_results/belts/belts.png

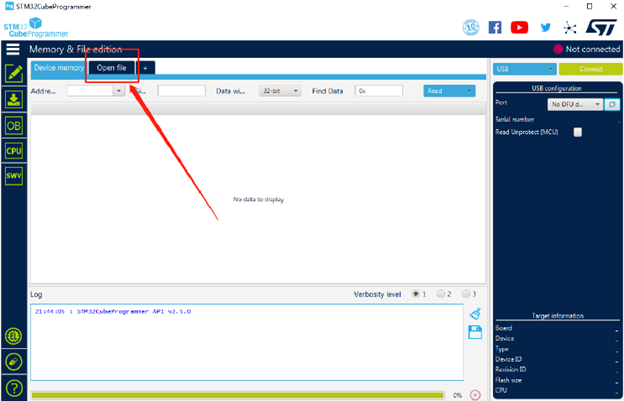
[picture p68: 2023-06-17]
tune-up/ebb_can/STMP2.png

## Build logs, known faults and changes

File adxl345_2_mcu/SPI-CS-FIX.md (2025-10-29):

# Orange Pi 3 LTS — фикс SPI1/CS (короткая инструкция)

Цель: включить аппаратный CS (ALT2) для SPI1, получить стабильный `/dev/spidev1.0` и корректную работу с устройствами (например, ADXL345).

## 1) Включить один spidev-оверлей
1. Открой `armbianEnv.txt`:
```bash
sudo nano /boot/armbianEnv.txt
```
2. Оставь только один SPI spidev-оверлей и одну CS:
```
overlays=spi-spidev1
param_spidev_spi_bus=0
param_spidev_spi_cs=0
```
3. Перезагрузка:
```bash
sudo reboot
```

Проверка:
```bash
ls /dev/spi*
gpio readall
```
- Должен появиться `/dev/spidev1.0`.
- Для MOSI.1/MISO.1/SCLK.1/CE.1 режим — ALT2 (не OFF).

## 2) Если CS всё ещё OFF — правка базового DTB
1. Бэкап и декомпиляция:
```bash
sudo cp /boot/dtb/allwinner/sun50i-h6-orangepi-3-lts.dtb /boot/dtb/allwinner/sun50i-h6-orangepi-3-lts.dtb.bak
sudo dtc -I dtb -O dts -o /boot/dtb/allwinner/sun50i-h6-orangepi-3-lts.dts /boot/dtb/allwinner/sun50i-h6-orangepi-3-lts.dtb
sudo nano /boot/dtb/allwinner/sun50i-h6-orangepi-3-lts.dts
```
2. В узле `spi@5011000`:
- `status = "okay";`
- корректный `pinctrl-0` на пины SPI1 + CS
- добавить `spidev@0` (или `spidev@1`, если используешь CS1):
```dts
spi@5011000 {
    compatible = "allwinner,sun50i-h6-spi","allwinner,sun8i-h3-spi";
    status = "okay";
    pinctrl-names = "default";
    pinctrl-0 = <0x31 0x32>; // phandle для spi1_pins и spi1_cs (могут отличаться в твоём DTS)
    #address-cells = <1>;
    #size-cells = <0>;

    spidev@0 {
        compatible = "armbian,spi-dev";
        reg = <0>;
        spi-max-frequency = <1000000>;
    };
};
```
3. Компиляция обратно и перезагрузка:
```bash
sudo dtc -I dts -O dtb /boot/dtb/allwinner/sun50i-h6-orangepi-3-lts.dts -o /boot/dtb/allwinner/sun50i-h6-orangepi-3-lts.dtb
sudo sed -i '/^overlays=.*spi/d' /boot/armbianEnv.txt   # убрать старые SPI-оверлеи
sudo reboot
```

## 3) Финальная проверка
```bash
ls /dev/spi*
gpio readall
```
- `/dev/spidev1.0` присутствует.
- MOSI/MISO/SCLK/CS — в ALT2.
- Тест-петля MISO↔MOSI даёт устойчивое эхо; реальное устройство отвечает без сбоев CS.

## Источник
- Форум Armbian (Orange Pi 3 LTS, SPI/CS, с примерами DTS/DTB):
  - https://forum.armbian.com/topic/28425-spi-problem-with-orange-pi-3-lts/#comment-181851

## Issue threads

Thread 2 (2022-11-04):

ошибка в статье Автоперезапуск сервиса klipper после включения принтера

obla4ko, 2022-11-04:
в статье указано что необходимо набирать команду "udevadm monitor – kernel – property – subsystem-match=usb"
она не выводит нужных параметров, правильная команда "udevadm monitor --kernel --property --subsystem-match=usb"

Tombraider2006, 2022-11-04:
спасибо за информацию, к сожалению статья не моя и я не  ее автор, я лишь указал ссылку как на интересный ресурс.

Closed 2022-11-04.

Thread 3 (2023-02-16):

Source of the Marlin firmware

axispod, 2023-02-16:
Hello.

Could you provide source files of your version of the Marlin firmware?

adequator, 2023-02-16:
https://github.com/FB-G6/Marlin

Tombraider2006, 2023-02-16:
response issued, request closed

Closed 2023-02-16.

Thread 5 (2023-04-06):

UART cable solder

ColdBeer72, 2023-04-06:
Hi!
In your page you say it's obsolete to desolder the resistors, but pictures show there is no resistor yet in the board...
I suppose those are pictures with older method used.
Do you mean I could directly solder the cable right in the upper side of the resistors (towards the drivers)?

Tombraider2006, 2023-04-06:
you god damm right. on pictures old method.

ColdBeer72, 2023-04-06:
Oh thanks!
So, it's really secure to solder the cable directly in the resistor (driver's side), isn't it?

Tombraider2006, 2023-04-06:
yes, this has already been tested by several users, everything works. it also eliminates the risk of breaking the track when soldering

Tombraider2006, 2023-04-06:
be sure to use hot melt adhesive to avoid breaking the wire from vibration during future operation of the printer.

Tombraider2006, 2023-04-06:
green side of course.

ColdBeer72, 2023-04-06:
Thanks again for the clarification

Closed 2023-04-06.

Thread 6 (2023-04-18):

Силиконка V6 и хотэнд

Sinicin1803, 2023-04-18:
Здравствуйте.
В разделе [Что купить](https://github.com/Tombraider2006/klipperFB6/blob/main/what_2_buy/readme.md) пункт 4 такой текст: "Сейчас проще - покупаем вид v6 [тут](http://alii.pub/6i4618)".
Я, как новичок и не специалист, выбрал именно  V6 ... по приезду посылки выяснилось, что правильней будет "V6 PT100 -Blue" ...
Прошу подправить этот момент.

А ещё, в первом пункте неплохо было бы хоть в кратце, для начинающих, разъяснить, для чего нужна модернизация/замена хотэнда. Я вот всё не мог понять, почему сопло и горло должны выставляться не так, как на стоковом, для чего эти танцы с бубнами... Пока в чате не поняли суть моего вопроса и не разъяснили. Вот это один из ответов, ну я думаю Вы, как специалист, сможете его правильно оформить.

"Потому что в стоковом не правильно собрана данная часть, производитель для чего то воткнул сопло мк8. Поэтому и горло на стоковом близко к кубику, что не есть хорошо! И трубка тефлоновая до конца проходит в горле, и при высоких температурах сопла, выше 230, данная трубка может оплавиться, что приведет к пробке!"

Я думаю, что у новичков будет меньше дурацких вопросов. Ведь нормальный человек всегда пытается понять, для чего он должен сделать именно так, а не иначе...

З.Ы. Спасибо за Ваши инструкции!

Tombraider2006, 2023-04-20:
по первому, исправил, по второму, подумаю как оформить нагляднее..

Closed 2023-05-06.

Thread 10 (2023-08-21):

Issues with Y Motor UART

nathanWilson81, 2023-08-21:
Is there anything new not noted in the drivers_uart pictures / folder? I am able to access the X and E just fine over UART following the directions, but the Y I have desoldered and resoldered about 5 times and every time, using the tmc.cfg that's there, it fails to access the Y over UART when I go to home the printer and the firmware crashes. Any help would be greatly appreciated!

nathanWilson81, 2023-08-22:
Closing. Turns out I just needed to desolder and resolder one more time to get it right

Closed 2023-08-22.

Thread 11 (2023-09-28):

Filament Change Macros - COUNTDOWN logs

KGOH, 2023-09-28:
Filament change macros introduces a `COUNTDOWN` macro to manage delays. The `COUNTDOWN` macro has comments that explain that log commands are not working as expected.

https://github.com/Tombraider2006/klipperFB6/blob/9cf48737535540b23bff91dbbf11cb5a2dbb0182/macros/filament.cfg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
https://github.com/Tombraider2006/klipperFB6/blob/9cf48737535540b23bff91dbbf11cb5a2dbb0182/macros/filament_biqu.cfg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
https://github.com/Tombraider2006/klipperFB6/blob/9cf48737535540b23bff91dbbf11cb5a2dbb0182/klipper_config_my/filament.cfg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

## Problem 1: Typo in Format Strings
The COUNTDOWN macro introduces issues with format strings in the code. It should use the correct format with the % operator.
Replace code like this: `"%s, %s", var1, var2`
with: `"%s, %s"%(var1, var2)`

## Problem 2: Non-Blocking Logs
Another issue with the COUNTDOWN macro is that `action_respond_info` commands are executed immediately after being sent, causing all logs to be printed immediately, even before the G4 dwells are executed.

From the [Klipper documentation on actions](https://www.klipper3d.org/Command_Templates.html#actions):

> Note that these actions are taken at the time that the macro is evaluated, which may be a significant amount of time before the generated g-code commands are executed

To fix this problem you can replace action_respond_info with the M118 respond command. This change requires enabling the M118 in the configuration.
For more details on configuring M118, refer to the [Klipper Config Reference](https://www.klipper3d.org/Config_Reference.html#respond).

## Possible fix:
Here's the updated code:
```klipper
[gcode_macro COUNTDOWN]
gcode:
    {% set timer = params.TIME|default(10)|int %}
    {% set message = params.MSG|default("Time: ") %}
    # countdown
    {% if timer > 60 %}
        {% for s in range(timer, 60, -10) %}
            M118 { "%s %s sec"%(message, s) }
            G4 P10000  # пауза 10 секунд
        {% endfor %}
        {% set timer = 60 %}
    {% endif %}
    {% if timer > 10 %}
        {% for s in range(timer, 10, -5) %}
            M118 { "%s %s sec"%(message, s) }
            G4 P5000   # пауза 5 секунд
        {% endfor %}
        {% set timer = 10 %}
    {% endif %}
    {% if timer > 0 %}
        {% for s in range(timer, 0, -1) %}
            M118 { "%s %s sec"%(message, s) }
            G4 P1000   # пауза 1 секунда
        {% endfor %}
    {% endif %}
    M118 { "%s finished"%(message) }
    BEEP
```

### Output:
When using COUNTDOWN with TIME=100, it will produce the following output:
```
$ COUNTDOWN TIME=100
echo: Time: 100 sec
echo: Time: 90 sec
...
echo: Time: 60 sec
echo: Time: 55 sec
...
echo: Time: 10 sec
echo: Time: 9 sec
...
echo: Time: 1 sec
echo: Time: finished
```

KGOH, 2023-09-28:
Refactored the `COUNTDOWN` macro to remove repetition. Less readable, but shorter :)

```klipper
[gcode_macro COUNTDOWN]
    gcode:
        {% set timer = params.TIME|default(10)|int %}
        {% set message = params.MSG|default("Time: ") %}

        {% set pause_durations = {60: (10000, -10), 10: (5000, -5), 0: (1000, -1)} %}

        {% for t, (pause_duration, delta) in pause_durations.items() %}
            {% if timer > t %}
                {% for s in range(timer, t, delta) %}
                    M118 { "%s %s sec"%(message, s) }
                    G4 P{ pause_duration }
                {% endfor %}    
                {% set timer = t %}
            {% endif %}
        {% endfor %}

        M118 { "%s finished"%(message) }
        BEEP
```

Closed 2023-09-29.

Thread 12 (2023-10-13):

Biqu H2

edombek, 2023-10-13:
Мне кажется или обновили версию экструдера и теперь она не влазит в крепления под него которые ты приложил? зхоидт с трудом и только с открытой лапкой филамента

Tombraider2006, 2023-10-13:
вы абсолютно правы и если почитаете более внимательно то увидите что добавлена версия 2VS и приложен архив к нему https://github.com/Tombraider2006/klipperFB6/blob/main/karas/5015v2s.rar

edombek, 2023-10-13:
А варианта под 4010 улитки нету?

Closed 2023-10-13.

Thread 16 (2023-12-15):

Замена стоковых моторов X/Y, распиновка контактов

sherbakov-37, 2023-12-15:
Добрый день.
Пытаюсь последовать Вашей рекомендации и поменять моторы на 42HS60-1504 от продавца duxe.ru. У меня мало опыта по работе с шаговыми двигателями. Никак не могу разобраться, какие контакты к какому пину на плате подвести.
В паспорте 42HS60-1504 указано, что обмотка A это черный и зеленый провод, обмотка B  красный и синий.
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
Контакты на плате слева направо 1B 1A 2A 2B.
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

Какой провод вести к 1A черный или зеленый? И какой провод к 1B?

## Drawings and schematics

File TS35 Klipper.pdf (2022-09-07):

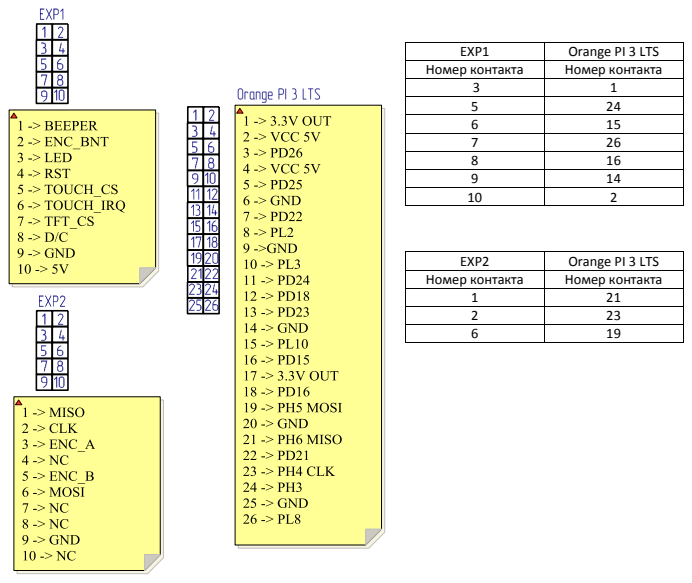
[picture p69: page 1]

EXP1 | Orange PI 3 LTS
Номер контакта | Номер контакта

5 | 24
6 | 15
7 | 26
8 | 16
9 | 14
10 | 2

EXP2 | Orange PI 3 LTS

1 | 21
2 | 23
6 | 19

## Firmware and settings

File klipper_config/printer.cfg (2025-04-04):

#[include timelapse.cfg] # если еще не настроили таймлапсы то будет ошбку выдавать. на первое время можно закоментировать.
#[include macro.cfg] # если не копировали этот файл то тоже закоментить

#### раздел подключения платы, сюда пишем результат команды ls /dev/serial/ после прочтения мануалов конечно же.
[mcu]
# Необходимо указать порт в соответствии со способом подключения платы управления принтера 
# к хосту, на котором запущен Klipper:
#
# Если плата подключена к хосту по интерфейсу UART (линии RXD, TXD):
#serial: /dev/ttyS3  ### Вариант для Orange Pi3 LTS и UART3 на пинах PD23,PD24
#
# Если плата подключена к хосту по шине USB, "чёрная плата" MKS Robin Nano4 v3.1, Nano6, и аналогичные на контроллерах STM32,
# то использовать идентификатор порта, полученный командой 
# ls /dev/serial/by-id
#serial: /dev/serial/by-id/usb-Klipper_stm32f405xx_380035001047323032383135-if00 
#
# Если MCU подключен к шине USB посредством микросхемы CH340, например, "красная" плата MKS Robin Nano4 v3.2, то использовать 
# идентификатор порта, полученный командой 
# ls /dev/serial/by-path
#serial: /dev/serial/by-path/platform-5101400.usb-usb-0:1:1.0 
serial: /dev/serial/<change_to_your_mcu_port_name> # строка-заглушка
restart_method: command

# датчик филамента
[filament_switch_sensor filament_detection]
pause_on_runout: True
#   When set to True, a PAUSE will execute immediately after a runout
#   is detected. Note that if pause_on_runout is False and the
#   runout_gcode is omitted then runout detection is disabled. Default
#   is True.
#runout_gcode:
#   A list of G-Code commands to execute after a filament runout is
#   detected. See docs/Command_Templates.md for G-Code format. If
#   pause_on_runout is set to True this G-Code will run after the
#   PAUSE is complete. The default is not to run any G-Code commands.
#insert_gcode:
#   A list of G-Code commands to execute after a filament insert is
#   detected. See docs/Command_Templates.md for G-Code format. The
#   default is not to run any G-Code commands, which disables insert
#   detection.
#event_delay: 3.0
#   The minimum amount of time in seconds to delay between events.
#   Events triggered during this time period will be silently
#   ignored. The default is 3 seconds.
#pause_delay: 0.5
#   The amount of time to delay, in seconds, between the pause command
#   dispatch and execution of the runout_gcode. It may be useful to
#   increase this delay if OctoPrint exhibits strange pause behavior.
#   Default is 0.5 seconds.
switch_pin: PA4
#   The pin on which the switch is connected. This parameter must be
#   provided.

#если у вас стоковая лента раскоментируйте три строки ниже и закоментируйте раздел [neopixel printhead] со всеми параметрами. 

#[output_pin caselight]
#pin: !PE6
#value: 1
[neopixel printhead]
pin: PE6
#   The pin connected to the neopixel. This parameter must be
#   provided.
chain_count: 3
#   The number of Neopixel chips that are "daisy chained" to the
#   provided pin. The default is 1 (which indicates only a single
#   Neopixel is connected to the pin).
color_order: GRB
#   Set the pixel order required by the LED hardware (using a string
#   containing the letters R, G, B, W with W optional). Alternatively,
#   this may be a comma separated list of pixel orders - one for each
#   LED in the chain. The default is GRB.
initial_RED: 0.15
initial_GREEN: 0.15
initial_BLUE: 0.15
#   See the "led" section for information on these parameters

[output_pin _Zummer]    # Если убрать подчеркивание из имени то выключатель станет видимым в панели(тогда не забудьте убрать подчеркивание из макроса ниже)
pin: PA2 
[gcode_macro beep]
gcode:
  SET_PIN PIN=_Zummer VALUE=1   # в завершающем коде слайсера напиши в конце beep 
  G4 P5000                      # и тогда после окончания печати он тебе пикнет 4 раза. это 5 секунд работы,
  SET_PIN PIN=_Zummer VALUE=0   # если хочется побольше то вместо 5000 поставь например 10000 будет пищать 10 секунд можно также вставить на замену филамента. на начало печати.

### раскомментируйте если установили модель чистки сопла 
#[gcode_macro Clean_nozle]
#gcode:
#   G1 X1 Y20 F10000 
#   G1 X1 Y130 F10000
#   G1 X1 Y70 F10000
#   G1 X1 Y130 F10000
#   G1 X1 Y70 F10000
#   G1 X1 Y130 F10000
#   G1 X1 Y20 F10000



#если у вас стоковая лед лента то этот раздел тоже нужно закоментрировать тут неопиксель подключен в разъем 3дтача
#[neopixel my_neopixel]
#pin: PA8
#   The pin connected to the neopixel. This parameter must be
#   provided.
#chain_count: 27
#   The number of Neopixel chips that are "daisy chained" to the
#   provided pin. The default is 1 (which indicates only a single
#   Neopixel is connected to the pin).
#color_order: GRB
#   Set the pixel order required by the LED hardware (using a string
#   containing the letters R, G, B, W with W optional). Alternatively,
#   this may be a comma separated list of pixel orders - one for each
#   LED in the chain. The default is GRB.
#initial_RED: 0.5
#initial_GREEN: 0.5
#initial_BLUE: 0.5
#initial_WHITE: 0.5
#   See the "led" section for information on these parameters.
### как ни странно инпутшейпинг такой неплохо работает на стоковой голове, нуждается в корректировке но работает.
[input_shaper]
shaper_type_x = ei
shaper_freq_x = 55
shaper_type_y = ei
shaper_freq_y = 70

########## cam Fan #########  вентилятор отсоса из камеры, пока не завязан ни на какие события, нуждается в макросах или дополнительных датчиках. в работе.
[fan_generic camera_Fan]
pin: PB0
#cycle_time: 0.05
kick_start_time: 0.5
#### раздел моторов, не знаешь не трогай! потрогал, не плачь!
[stepper_x]
step_pin: PE3
dir_pin: !PE2
enable_pin: !PE4
microsteps: 32
rotation_distance: 40
endstop_pin: !PA15
position_endstop: 1
position_max: 255
homing_speed: 40

[stepper_y]
step_pin: PE0
dir_pin: !PB9
enable_pin: !PE1
microsteps: 32
rotation_distance: 40
endstop_pin: !PD2
position_endstop: 1
position_max: 220
homing_speed: 40

[stepper_z]
step_pin: PB5
dir_pin: !PB4
enable_pin: !PB8
microsteps: 32
rotation_distance: 8
endstop_pin: !PC8
position_endstop: 0.5
homing_speed: 10
second_homing_speed: 2
position_min: -20
position_max: 200

[extruder]
step_pin: PD6
dir_pin: PD3
enable_pin: !PB3
microsteps: 16
rotation_distance: 7.815
max_extrude_only_distance: 1400.0
nozzle_diameter: 0.400
filament_diameter: 1.750
heater_pin: PE5
sensor_type: ATC Semitec 104GT-2
#sensor_type: Generic 3950 # если меняли на 3950 закомментируй строчку выше, раскомментриуй эту
sensor_pin: PC1
control: pid
pid_Kp: 14.669
pid_Ki: 0.572
pid_Kd: 94.068
min_temp: 0
max_temp: 320

[heater_bed]
heater_pin: PA0
sensor_type: EPCOS 100K B57560G104F
sensor_pin: PC0
control: pid
pid_Kp: 71.783
pid_Ki: 1.977
pid_Kd: 651.428
min_temp: 0
max_temp: 130
#### кулер обдува модели
[fan]
pin: PB1
#off_below: 0.25
#shutdown_speed: 0.0
##### кулера обдува платы и обдува хотенда. 
[heater_fan nozzle_fan]
pin: PC14
#kik_start_time: 0.1
shutdown_speed: 1.0
heater: extruder
heater_temp: 50
fan_speed: 1.0
#### выключение по простою, по мне так не очень нужно поэтому задокументировано. 
#[idle_timeout]
#timeout: 1200
#gcode:
#  M84
#  SHUTDOWN_MACHINE
#### датчики различных температур. можно поменять название, главное вместо пробелов поставить подчеркивание
[temperature_sensor orange_pi]
sensor_type: temperature_host
min_temp: 10
max_temp: 100


#Если у вас красная плата  Robin Nano4 3.2 то вам надо закоментировать следующий раздел!

[temperature_sensor mcu_temp]
sensor_type: temperature_mcu
min_temp: 0
max_temp: 100



## без нужды не трогать, дальше сами знаете...
[safe_z_home]
home_xy_position: 1,1                                                       # CAUTION! Depends on probe X/Y offset
z_hop: 10
move_to_previous: True                                                       # Return back ~X0/Y0 after Z0 at center
z_hop_speed: 20
speed: 200
####  регулировка откатов здесь. если вы заменили стоковое горло  то оставляйте так,
####   если заменили шестерню и\или деталь фидера, продолжайте настройку, можно лучше, но ненамного
[firmware_retraction]
retract_length: 0.8
retract_speed: 25
unretract_extra_length: 0
unretract_speed: 25

# исключение обьектов, прикольная вещь, в куре достаточно отключить комбинг чтоб работало ну и  Должно еще быть прописано в moonracker.cfg вот это: [file_manager] enable_object_processing: True. 
[exclude_object]
#### а вот сюда вообще не надо лезть. как разберетесь лезьте на здоровье, но я предупредил)
[printer]
kinematics: corexy
max_velocity: 400
square_corner_velocity: 5.0
max_accel: 8000
#max_accel_to_decel: 4000
max_z_velocity: 25
max_z_accel: 100
### регулировка положения стола
[bed_screws] # BED_SCREWS_ADJUST
screw1: 28,31
screw1_name: front left screw
screw2: 228,31
screw2_name: front right screw
screw3: 228,181
screw3_name: back right screw
screw4: 28,181
screw4_name: back left screw
speed: 150
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

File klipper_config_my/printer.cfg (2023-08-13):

[include shell_command.cfg]
[include timelapse.cfg]
[include macro.cfg]
[include tmc.cfg]
[include clean.cfg]
[include filament.cfg]
[include adaptive_bed_mesh.cfg]
[include fluidd.cfg]
[include vibr_calibrate.cfg]


[delayed_gcode bed_mesh_init] 
initial_duration: .01
gcode: BED_MESH_PROFILE LOAD=default

[gcode_shell_command shaper_calibrate]
command: bash /home/pi/printer_data/config/shaper_calibrate.sh
timeout: 600.
verbose: True
[gcode_shell_command plot_graph]
command: bash /home/pi/printer_data/config/scripts/plot_graphs.sh
timeout: 500.0
verbose: True
[respond]

[gcode_arcs]

[adxl345]
cs_pin: PC15
spi_software_sclk_pin: PB13

spi_software_mosi_pin: PC3

spi_software_miso_pin: PC2
axes_map: x,-y,-z
[resonance_tester]
accel_chip: adxl345
probe_points:
    125, 100, 20

[mcu host]
serial: /tmp/klipper_host_mcu

[fan_generic camera_Fan]
pin: PB0
cycle_time: 0.05
kick_start_time: 0.5





[filament_switch_sensor filament_detection]
pause_on_runout: True
#   When set to True, a PAUSE will execute immediately after a runout
#   is detected. Note that if pause_on_runout is False and the
#   runout_gcode is omitted then runout detection is disabled. Default
#   is True.
runout_gcode: beep
#   A list of G-Code commands to execute after a filament runout is
#   detected. See docs/Command_Templates.md for G-Code format. If
#   pause_on_runout is set to True this G-Code will run after the
#   PAUSE is complete. The default is not to run any G-Code commands.
#insert_gcode:
#   A list of G-Code commands to execute after a filament insert is
#   detected. See docs/Command_Templates.md for G-Code format. The
#   default is not to run any G-Code commands, which disables insert
#   detection.
#event_delay: 3.0
#   The minimum amount of time in seconds to delay between events.
#   Events triggered during this time period will be silently
#   ignored. The default is 3 seconds.
#pause_delay: 0.5
#   The amount of time to delay, in seconds, between the pause command
#   dispatch and execution of the runout_gcode. It may be useful to
#   increase this delay if OctoPrint exhibits strange pause behavior.
#   Default is 0.5 seconds.
switch_pin: PA4
#   The pin on which the switch is connected. This parameter must be
#   provided.


[output_pin _Zummer]
pin: PA2 

[gcode_macro beep]
gcode:
  SET_PIN PIN=_Zummer VALUE=1   # в завершающем коде слайсера напиши в конце beep 
  G4 P5000                      # и тогда после окончания печати он тебе пикнет 4 раза. это 5 секунд работы,
  SET_PIN PIN=_Zummer VALUE=0 


[output_pin caselight]
pin: !PE6
value: 1


[input_shaper]

########## cam Fan #########

#[fan_generic camera_Fan]
#pin: PB0
#cycle_time: 0.05
#kick_start_time: 0.5







[stepper_x]
step_pin: PE3
dir_pin: !PE2
enable_pin: !PE4
microsteps: 16
rotation_distance: 40
endstop_pin: !PA15
position_endstop: 1
position_max: 255
homing_speed: 40

[stepper_y]
step_pin: PE0
dir_pin: !PB9
enable_pin: !PE1
microsteps: 16
rotation_distance: 40
endstop_pin: !PD2
position_endstop: 1
position_max: 220
homing_speed: 40

[stepper_z]
step_pin: PB5
dir_pin: !PB4
enable_pin: !PB8
microsteps: 32
rotation_distance: 8
#endstop_pin: !PC8
endstop_pin: probe:z_virtual_endstop
#position_endstop: 0.5
homing_speed: 40
second_homing_speed: 2
position_min: -10
position_max: 200

[extruder]
step_pin: PD6
dir_pin: PD3
enable_pin: !PB3
microsteps: 16
rotation_distance: 3.4334
max_extrude_only_distance: 1400.0
nozzle_diameter: 0.400
filament_diameter: 1.750
heater_pin: PE5
sensor_type: Generic 3950
sensor_pin: PC1
min_temp: 0
max_temp: 320
pressure_advance = 0.042
min_extrude_temp: 0

[heater_bed]
heater_pin: PA0
sensor_type: EPCOS 100K B57560G104F
sensor_pin: PC0

min_temp: 0
max_temp: 130
[verify_heater heater_bed]
max_error: 130
check_gain_time: 80

[fan]
pin: PB1
off_below: 0.10
kick_start_time: 0.5

[heater_fan nozzle_fan]
pin: PC14
#kik_start_time: 0.1
shutdown_speed: 1.0
heater: extruder
heater_temp: 50
fan_speed: 1.0



[temperature_sensor orange_pi]
sensor_type: temperature_host
min_temp: 10
max_temp: 100

[temperature_sensor mcu_temp]
sensor_type: temperature_mcu
min_temp: 0
max_temp: 100



[firmware_retraction]
retract_length: 0.4
retract_speed: 30
unretract_extra_length: 0
unretract_speed: 30

[mcu]
#serial: /dev/serial/by-id/usb-Klipper_stm32f407xx_12345-if00
serial: /dev/ttyS3
restart_method: command
[mcu host]
serial: /tmp/klipper_host_mcu

[printer]
kinematics: corexy
max_velocity: 800
square_corner_velocity: 5.0
max_accel: 8000
max_accel_to_decel: 6000
max_z_velocity: 25
max_z_accel: 100

[bed_screws] # BED_SCREWS_ADJUST
screw1: 26,40
screw1_name: front left screw
screw2: 225,40
screw2_name: front right screw
screw3: 225,192
screw3_name: back right screw
screw4: 26,192
screw4_name: back left screw
speed: 150

[bltouch]

sensor_pin: ^PC4
control_pin: PA8
y_offset: 34.6
#z_offset: 2.0
x_offset: 24.4
speed: 10.0
samples: 3
samples_result: median
sample_retract_dist: 3.0
samples_tolerance: 0.15
samples_tolerance_retries: 3


[safe_z_home]
home_xy_position: 103,95                                                      # CAUTION! Depends on probe X/Y offset
z_hop: 10
move_to_previous: True                                                       # Return back ~X0/Y0 after Z0 at center
z_hop_speed: 10
speed: 50
[gcode_macro G29]
gcode:
    BED_MESH_CLEAR
    G28
    BED_MESH_CALIBRATE
    BED_MESH_PROFILE SAVE=name
    SAVE_CONFIG
    BED_MESH_PROFILE LOAD=name

[bed_mesh]
speed: 40
horizontal_move_z: 5
mesh_min: 30,40
mesh_max: 245,185
probe_count: 7,5
algorithm: bicubic
fade_start: 1
fade_end: 7
[screws_tilt_adjust]                                                          
screw4: 5,5                
screw4_name: front left screw
screw1: 210,5                             
screw2: 210,170             
screw2_name: back right screw
screw3: 5,170        
screw3_name: back left screw
speed: 150
screw_thread: CW-M4


[exclude_object]


[virtual_sdcard]
path: ~/printer_data/gcodes

[pause_resume]

[display_status]

[gcode_macro SHUTDOWN_MACHINE]

gcode:
    {action_call_remote_method("shutdown_machine")}

[gcode_macro PAUSE]
rename_existing: BASE_PAUSE
gcode:
    SAVE_GCODE_STATE NAME=PAUSE_state
    BASE_PAUSE
    {% set X = params.X|default(10) %}
    {% set Y = params.Y|default(180) %}
    {% set E = params.E|default(2) %}
    {% set Z = params.Z|default(150) %}
    G91
    G1 E-{E} F2100
    G1 Z{Z}
    G90
    G1 X{X} Y{Y} F6000

[gcode_macro RESUME]
rename_existing: BASE_RESUME
gcode:
    {% set E = params.E|default(2) %}
    G91
    G1 E{E} F2100
    G90
    RESTORE_GCODE_STATE NAME=PAUSE_state MOVE=1
    BASE_RESUME

[gcode_macro CANCEL_PRINT]
rename_existing: BASE_CANCEL_PRINT
gcode:
    TURN_OFF_HEATERS
    CLEAR_PAUSE
    SDCARD_RESET_FILE
    BASE_CANCEL_PRINT
    M106 S0
    G91
    G1 Z5
    G90
    G1 X5 Y105
    M84

[gcode_macro PID_E]
gcode:
  {% set T = params.T|default(255) %}
  PID_CALIBRATE HEATER=extruder TARGET={T}

[gcode_macro PID_B]
gcode:
  {% set T = params.T|default(80) %}
  PID_CALIBRATE HEATER=heater_bed TARGET={T}

#*# <---------------------- SAVE_CONFIG ---------------------->
#*# DO NOT EDIT THIS BLOCK OR BELOW. The contents are auto-generated.
#*#
#*# [extruder]
#*# control = pid
#*# pid_kp = 23.357
#*# pid_ki = 0.979
#*# pid_kd = 139.268
#*#
#*# [heater_bed]
#*# control = pid
#*# pid_kp = 68.579
#*# pid_ki = 1.566
#*# pid_kd = 750.936
#*#
#*# [stepper_z]
#*# position_endstop = 0.250
#*#
#*# [input_shaper]
#*# shaper_type_x = mzv
#*# shaper_freq_x = 69.2
#*# shaper_type_y = mzv
#*# shaper_freq_y = 51
#*#
#*# [bltouch]
#*# z_offset = 0.550
#*#
#*# [bed_mesh default]
#*# version = 1
#*# points =
#*# 	-0.058750, -0.085000, -0.053750, -0.041250, -0.018750, -0.028750, -0.075000
#*# 	0.020000, 0.006250, -0.010000, -0.018750, -0.066250, -0.077500, -0.026250
#*# 	0.047500, 0.032500, 0.003750, 0.027500, -0.005000, -0.028750, 0.017500
#*# 	0.035000, 0.061250, 0.043750, 0.040000, -0.003750, -0.017500, 0.016250
#*# 	0.076250, 0.081250, 0.063750, 0.055000, 0.018750, -0.007500, -0.010000
#*# x_count = 7
#*# y_count = 5
#*# mesh_x_pps = 2
#*# mesh_y_pps = 2
#*# algo = bicubic
#*# tension = 0.2
#*# min_x = 30.0
#*# max_x = 244.98000000000002
#*# min_y = 40.0
#*# max_y = 185.0

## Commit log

2022-09-07 Update printer.cfg
    поправил скорости парковки, закоментил отключение по простою.
    [printer.cfg]
2022-09-07 Update printer.cfg
    по умолчанию посветка включена
    [printer.cfg]
2022-09-11 Add files via upload
    изменил шаги моторов для того чтобы убрать скрип при передвижении на скоростях около 120-150 мм\сек
    [printer.cfg]
2022-09-14 Update printer.cfg
    привел к стоковому состоянию, закоментриовал неопиксель подсветку.
    [printer.cfg]
2022-09-18 исправление ошибок, добавлены коментарии для стока
    [printer.cfg]
2022-09-18 добавка макросов к лентам подсветки.
    работать будет только с адресными лентами. требует правки под ваше количество светодиодов. выложено исключительно для примера.
    [macro.cfg]
2022-09-19 убрал часть кода
    убрал часть кода и написал пояснялки
    [macro.cfg]
2022-09-19 добавил описание
    начал добавлять описание к параметрам, если не понятно и требует дополнения пишите.
    [printer.cfg]
2022-09-19 добавил ссылки.
    немного обновил описание, надеюсь не последний раз
2022-09-29 Update printer.cfg
    убрал ошибку в описании имени прошивки
    [printer.cfg]
2022-09-30 Update README.md
    добавил ссылку на клипперскрин для малинки
2022-10-02 обнова
    [printer.cfg, tmc.cfg]
2022-10-02 добавил описание
2022-10-12 структуризация
2022-10-12 структуризация 0.2
2022-10-12 добавлен раздел bme280
2022-10-12 добавил источник на всякий случай если у кого не взлетит.
2022-10-12 уфф.. бета 2..0
2022-10-12 до кучи и тут обновим
2022-10-16 поправил логику изложения материала
2022-10-16 несущественные правки
2022-10-17 альфа 0
2022-10-17 добавил общий вид
2022-10-17 добавлен раздел placement
2022-10-17 5 пункт - done
2022-10-19 добавил второй вариант крепления
2022-10-20 макрос на пищалку добавил, убрал пищалку из панели
    [printer.cfg]
2022-10-21 добавка стартовых конечных кодов
2022-10-21 добавил макрос clean_nozle
    [printer.cfg]
2022-10-23 орфографические правки
2022-10-23 мелкие исправления
2022-10-23 подправил юзабилити
2022-10-23 юзабилити, радел timelapse
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2022-10-24 макрос бонус от ch1stov
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2022-11-01 ссылка на дешевый бикью
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2022-11-03 и еще поправил разметку
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2022-11-07 добавил инфы про плагин куры)
2022-11-09 обновление модели от 7 ноября
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2022-11-10 правки 5 и 7 дюймов
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2022-11-19 ссылки на провода, орфография.
2022-11-19 дополнил про "тихий" режим
2022-11-19 правка болтиков 2 на 2.5
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2022-11-20 макросы
    [beep.cfg]
2022-11-20 правка кода
    [filament.cfg]
2022-11-20 вариант biqu добавил
    [filament_biqu.cfg]
2022-11-20 правка ошибки кода
    [filament.cfg, filament_biqu.cfg]
2022-11-21 баги..(
    [filament.cfg, filament_biqu.cfg]
2022-11-22 добавил ссылку на инструкцию по горлу
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2022-11-25 правки коментариев
    [printer.cfg]
2022-11-25 ссылка на управление питанием
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2022-11-26 исправил ссылки
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2022-11-26 добавлен bltouch под 1 карася
    [Karas_niz_bltouch.stl]
2022-11-26 держатель блтач
    [BLTouch_holder.stl]
2022-11-27 обновление stl
    [Karas_niz_bltouch.stl]
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2022-12-04 printer_data - достали...
    [printer.cfg]
2022-12-06 раздел в процессе написания
2022-12-06 Update printer.cfg
    чутка правок на ночь
    [printer.cfg]
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2022-12-07 добавил руководство по экранам.
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2022-12-08 исправления
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2022-12-10 исправлен архив 5015
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2022-12-12 версия 12.12 5015 карась
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2022-12-18 bltouch на стоковую голову
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2022-12-21 объеденение инфы про экструдеры
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2022-12-21 майнсейл тоже заработал rgb
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2023-01-02 вибра и втулки правка
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2023-01-03 правки pid
    [printer.cfg]
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2023-01-21 Conexión de una impresora a través de UART
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2023-01-25 update термобарьер теперь можно купить нормальный
2023-01-26 еще одна инструкция по смазке
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2023-01-30 Востановление печати после сбоя питания
    [power_loss.cfg]
2023-01-30 Восстановление печати после сбоя питания
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2023-02-02 бекап
    [printer.cfg]
2023-02-10 правка для клипперскрин
    [filament_biqu.cfg]
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2023-03-05 ремарка про экструдер VS
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2023-03-24 дабавлен вариант головы ZOHAN
2023-03-24 выделил ман по шагам экструдера отдельно
2023-03-25 правка ссылка на горло
2023-03-30 Update readme.md
    исправлен косяк с добавлением камеры
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2023-04-02 опции вращения камеры в клипперскрин
2023-04-02 орфография, беспощадная ты сука
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2023-05-01 добавлена ссылка на гит разработчиков
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2023-05-06 Update printer.cfg
    Небольшое предложение по переключателю стоковой ленты подсветки. В таком варианте переключатель в состоянии Вкл когда лента горит
    [printer.cfg]
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2023-05-15 очепятка - исправил
2023-05-16 тест мотор вместо сервы
2023-05-21 обновления ссылок на ресурсы
2023-06-04 Update newby.md
    про трубку термобарьера
2023-06-17 макрос окраски respond
    [macro.cfg]
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2023-06-23 спец для дмитрий задирако
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2023-07-24 графики в телеграм бот
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2023-07-24 правки кода убрал перенос строки dos
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2023-07-25 замена на актуальную версию
    [fluidd.cfg, macro.cfg, moonraker-obico-update.cfg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]
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2023-09-28 фикс макроса
    [filament.cfg, filament_biqu.cfg]
2023-10-01 держатель щетки под вулкан хотенд
    [dryer_vulcano.stl]
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2024-03-12 Update readme.md
    Добавил заголовки
2024-08-19 [FIX] max_accel_to_decel устарел
    Опция max_accel_to_decel устарела и пугает людей ошибками
    [printer.cfg]
2025-01-26 fix microsteps and rotation distance for stock configuration
    [printer.cfg]
2025-04-04 мини-инструкция по mcu serial
    Более полное описание секции [mcu] serial прямо в файле конфигурации. Дефолтная строка написана так, чтобы сообщени об ошибке отсылало к правке printer.cfg.
    Секция перенесена в "голову" файла конфигурации
    [printer.cfg]
2025-04-04 fix typo in rotation distance
    [printer.cfg]
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
